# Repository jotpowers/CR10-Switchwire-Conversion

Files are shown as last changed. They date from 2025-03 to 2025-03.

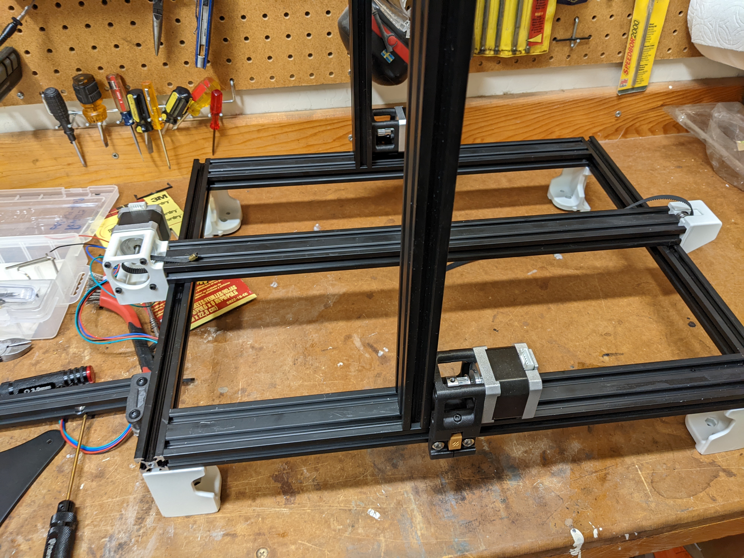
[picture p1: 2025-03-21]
photos/switchwire-test1.jpg

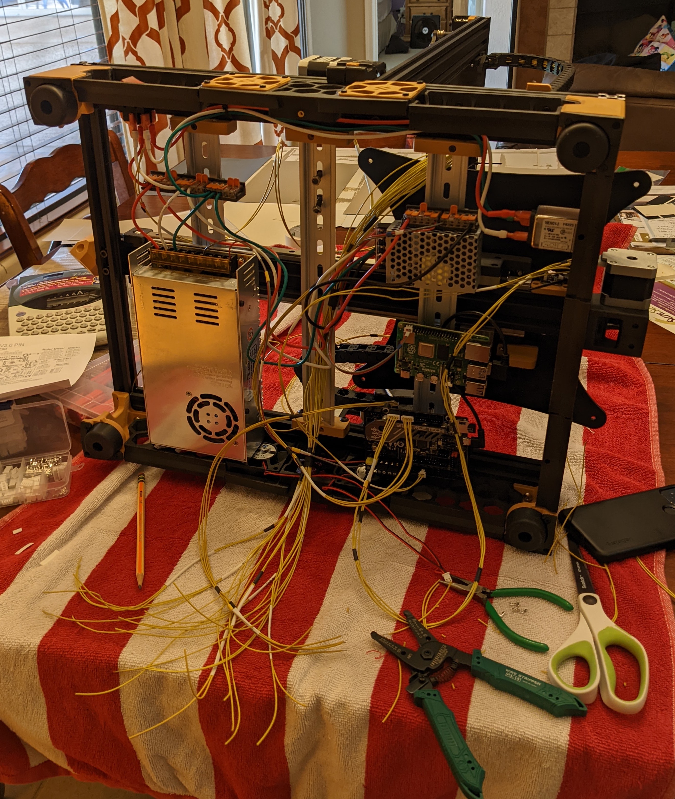
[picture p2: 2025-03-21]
photos/switchwire-electronics-bay-wiring.jpg

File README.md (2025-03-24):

# Introduction

Back in ~2017 my 16 year old son saved his money up and bought and assembled a 300mm Creality CR-10 [1] . It was the first of the post-kickstarter systems, so had some rough edges.  There are plenty of things I don't like about it, but for its cost and time, it's a pretty amazing machine.  When COVID hit and I started printing a bunch of faceshield pieces for Masks4Docs it was a workhorse. But, I kept doing more and more mods to it, but wasn't very reliable.  Finally the SKR controller board (that had replaced the original) broke.  (One day both the bed and hotend thermistors slowly started reading strange numbers).  At that point I was done, and thus began me building a Voron 2.4.

But, I have this perfectly good frame, with motors and some spare parts left over from my 2.4 build...

So I decided to build a CR10, Switchwire.  This repo will be my working notes.

# Design goal

Keep as much of the CR10 stock as possible.  Ideally, you would be able to reverse this mod and have a CR10 back.  Also, ideally, you would never want to.

* Stock frame
* Existing motors  (except extruder, which is going direct drive)
* 12V power supply (which results in a bunch of downstream dependencies)
  * Yeah, this didn't work out.  I couldn't figure out why the fans wouldn't spin up and various other issues.  Turns out, even when turned all the way up, this 12V power supply was putting out like 10.3V.  I replaced it with [this one from Amazon.](https://www.amazon.com/dp/B0131UU9E2?ref_=ppx_hzsearch_conn_dt_b_fed_asin_title_1)
* DC bed heater 

But, I'm not going to be unreasonable here.

* I had already replaced the stock CR10 hotend a long time ago.  I'll go with Afterburner/Stealthburner here.
  * I went with Stealthburner as well as TAP.
* Going to run klipper
  * This means I need a Raspberry Pi
  * Also I'll probably have a dedicated 5V power supply

# Status as of 2022

* The electronics are mostly working and I have a "wire harness" in.
* Hotend is assembled, but not wired up.
* Klipper boots and is happy
* Can buzz all the motors
* Have temperature from both thermistors
* Can heat the bed

# Current status (as of March of 2025)

Well, that was a slow couple of years.  Just got to the annoying debug/triage part and it just sat around.  But my son was in town and we wanted to try to get TPU printing, so pushed forward.

* It's pushing plastic!  

# Progress Pictures
You can see the progress over in the [progress pics](progress.md).

# Upcoming problems

* Bed height/leveling is going to be an issue.  Can't pull the bed down too low against the springs because the bolts can hit the cable chain.  Might need shorter bolts.
  * Think I solved this.  Need to document.

# Things to document
* Thicker XZ pulley's created
* Find power supply holders
* The TAP switchwire mount

# Iteration

Initially I was going to try to reconfigure the frame to get as close to the default SwitchWire as possble.  But that was resulting in some compromises and would have resulted in drilling the existing frame a few times.  Not a deal breaker since extra holes wouldn't prevent it from being reversible, but the orientation of the frame pieces also ended up resulting in challenges with how things would mount and probably having to go modify most of the XZ axies.  

Then someone on Discord had mocked up a SwitchWire with the original frame configuration, and used the Trident feet/skirts.  That had the advantage of making the XZ pretty stock, and only requiring mods to the Y.  There were already some mods that did something similar, so went down that route.

# Y-axis

I'm going to use the [Ender_SW](https://github.com/boubounokefalos/Ender_SW) mod for this.  The reason is that I don't have a spare 2020 aluminum extrusion to run the stock SwitchWire, and I was starting to run into all sorts of issues trying to go with 2040 aluminum extrusion that is from the CR10 frame.  Since that's closer to the stock CR10 and it simplifies XZ axis, I opted to mod the Y-axis and go stock on the XZ axis.  Especially since this Y-axis mod is a two linear rail setup, which has to be twice as good as one, right?

* You do want to add stops for the Y-axis lineral rails since the expectation was they go until they hit the front idler, and that's what prevents the carriages from coming off the rails.  I just printed some extra Z-axis stop pieces and put them at the front.

## Things you have to change

* You need to use an m5 tap on the ends of the Y-axis gantry 2040 aluminum extrusion.  Maybe not need, but it's what I did.  It helps with the motor/idler mouting.
* You'll need to drill holes in the bed plate to center it on the new gantry.  See the [progress photos](progress.md).

### Problems this causes for you

* This whole system sits lower than the stock Switchwire.  
  * This means that the carriages will now sit lower than the deck plate you want to install (to get cereal'd).  
    * My solve this this was to modify the DIN rail mounts to allow the DIN rails to be lower.  I should probably have just CAD'd them from scratch, but I didn't, so they have some small bits of extra "character"
      * But, this now meant that if you use the (new and better) Trident DIN mounts, the 12V power supply sits lower than where the bottom panel lines up.  
        * So, I used the (inferior but shorter) 2.4r1 PS DIN mounts to recover that height.

# XZ-axis

The first problem here is that the existing 2020 that used to hold the X-axis is too wide.  If you try to reuse it, then the belts from the motors would hit it.  So you'd have to modify the motor mounts to go further out.  Then, the pulleys at the top need to be modified.  Then... I decided I wasn't ready for that level of modification yet.  So, you can either chop down your existing 2020 (which is *not* reversible) or order a new one.  

## How I solved this
* I bought a 38cm piece of 2020 extrusion from Misumi.  I might have measured that after a few drinks though, because I should have bought a 39cm piece of 2020 extrusion.  It works, but now you know.

Well, while I was waiting for StealthBurner to come out of beta so it could have a toolhead PCB so I didn't have to wire things, I decided to finally just belt up XZ, because it would be easy.  This is the first place that the difference between 2020 and 3030 has bitten me (that I know of so far).  It makes subtle changes in alignment, so that suddenly the belt wouldn't line up from the top Z idlers down to/past the X gantry.

## How I'm hoping to solve this (because I haven't yet)

I went ahead and pulled the piece out of the cad and then created a parameter for thickness and added 10mm.  It's a big chonky thing, and I now need longer bolts, but it looks like it will work.  It's so ugly though, will probably need a redesign.  Given that, haven't added CAD and STL, but available upon request.

# Below the belt (aka skirts & electronics)

* Went with Trident feet to get height
* Will need to figure out skirts, especially since I went with a split switch and power inlet, because I hate reaching around.  Take that however you will.
  * I went ahead and did this, and I can tell you it was worth it.  The side switch should be stock.

In general the footprint is really close to the 250mm Trident for the front and back, and the 350mm Trident for the sides.  

## What I did

### Rear skirts
* Split the power inlet from the switch.  
  * I could have just blanked out the switch, but that would have looked meh, so I decided to have it be a keystone slot instead.  But, if you look at the CAD on the keystone slots, it's a bit more finicky than you would expect (not just rectangular holes), so instead I blanked one of those and then put the power inlet there. 
    * This means the power switch is now on the right (as you look at the machine), so to use the original keystone plate, you need to mirror it to be on the left.
  * The footprint is a little narrower than the 250, so I scaled the center rear panel (unlocked, so only one dimension) from 117mm to 100mm on the X axis.
    * But, things you don't think about.  The bolts for the center rail run through the middle of this extrusion.  Your drop in nuts won't hit it, but the slight raised part on the skirt, meant to slide into that slot, now slightly hits those bolts.  Means that you end up having to work a little extra hard to get the bolts in that hold that piece of the skirt.

### Side skirts

* I filled and then cut the front right skirt to include the switch.  Yes, I'm glad I did it, having the switch easy to access is so much better.
* The footprint is again, slightly smaller, so I scaled one of the skirt pieces down to ~124mm in the long axis to get it to fit.
* I *despise* VHB tape, so I went with the new (2.4r2) mounts for the fans and the blank fan pieces.  This works great, except...
  * The mounts for the A/B motors interferes with the fan cover in one of the corners of one plate on each side.  It's not elegant, but I just trimmed and filed that to allow it to fit in.  Was able to screw them in with flat head screws, but it's a bit hacky. (Visible in the [progress picks](progress.md))

### Electronics

I had a 1 meter piece of DIN rail.  Since the space is 32cm (I think) across, I actually went with three, and have the center one with a cable raceway to make it all nice and pretty.

Note on cable raceway: I tried the printed ones, but ABS is just too brittle for them and they would break, so broke down (heh) and bought them from Amazon.

# Extra/modified CAD items

* Wago mount for bed wiring
* Lowered DIN mounts
* Side skirt with switch
* Back power inlet
* Y-axis tensioner, now with more attitude
* More linear rail stops
* SKR holder for DIN mount

# Stuff you have to buy

* 20t pulley
* gates 6mm belt (had this as a spare from 2.4 build)
* bearings
* various screws (will probably detail later)
* filament (for printing parts)
* Keybak (13 oz)
* linear rails
* wire (wow, a lot of it)
* cable chains
* heatsets
* 5 MGNH12 rails.  
  * The biggest I could find easily were 400mm.  On Z I think you could go to 450, so maybe in the future I'll change that since it would just be a rail swap and not much other change. 
  * You need 4x 400
  * 1x 350 for the X axis gantry
* JST-PH 2.0 connectors (for motors) [Amazon link](https://smile.amazon.com/gp/product/B09DBHG6NW/ref=ppx_yo_dt_b_asin_title_o07_s00?ie=UTF8&psc=1)

## Stuff you might have
* Blue loctite

## Not really necessary, but I did anyway

* 5v PSU
* Power inlet and switch

# CAD

In general my goal is to change as few things as possible.  I might actually copy all of the CAD files here in the future to simply give you one place to download them, but not for now.  But, here are a list of things I changed:

* [Stealth Idler](STL/y-gantry/ender_sw_stealth_idler.stl)
  * I provide the f3d and step files.  This mod addressess two issues:
    * I wanted to be able to put screws into a threaded m5 hole in the 2040
    * I did not like the look of the standard idler.  Given the recently released StealthBurner, I figured I'd do a bad version of that for the outer idler.  The inner remains unchanged.
* [Mounts](STL/mounts/)
  * Because the Switchwire assumes you're mounting everything to the extrusions, and I'm using DIN, I needed a bracket for the SKR to mount to the DIN holder.  This bracket isn't perfect, but it's close enough for now.
  * Also, while I was at it, I made one for an Arduino Uno.  This is really to be a secondary MCU for my 2.4, but I'm putting it here for now, because why not.
* [Offset DIN mount](STL/mounts/offset-din-rail-mount.stl)
  * As described above, in the "cascading consequences" of the Y-axis, here are the files for the offset DIN mounts.  A little ugly because I didn't want to have to CAD in the profile of the DIN rail.  I should really learn how to start with a body to make that easier.
* [Power Skirts](STL/skirts)
  * This contains the files for both the power inlet (with keystone) and the (right) side skirt with a hole for the switch.  I made some minor mods on the power inlet after I printed mine, to correct some issues, but haven't printed/tested it, so buyer beware.

# Helpful Hints

* There is currently a SKR Mini E3 V3 config file for the switchwire.  As a result, when you get done fixing various pin definitions in printer.cfg, klipper just shuts down complaining about ADC pin.
  * I think it's the sensor pin on the heater bed that changed between V2 and V3.  New sensor pin is PC4.

* I am inordinately happy with the fact that I have the original CR10 display working now. It has terrible resolution.  It's a bad size.  But I love it because it maintains the original (even if I now have to go buy/make a longer ribbon cable).  Here are the values I used for the config to get the display to work.  

<pre>
[display]
lcd_type: st7920
cs_pin: PB8
sclk_pin: PB9
sid_pin: PD6
encoder_pins: ^PA10, ^PA9
#encoder_pins: ^EXP1_5, ^EXP1_3
click_pin: ^!PA15
#kill_pin: ^!EXP2_8

[output_pin beeper]
pin: PB5
</pre>

# Notes

[1] Officially it's CR-10, not CR10, but no one really cares and the latter is more commonly used, so I'll go with that going forward.  Or randomly.

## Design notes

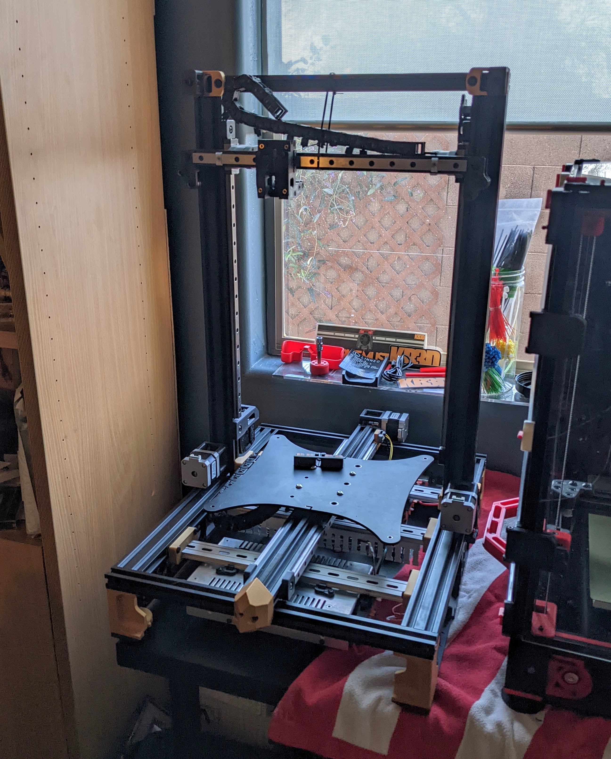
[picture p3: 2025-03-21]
photos/switchwire-electronics-mounted.jpg

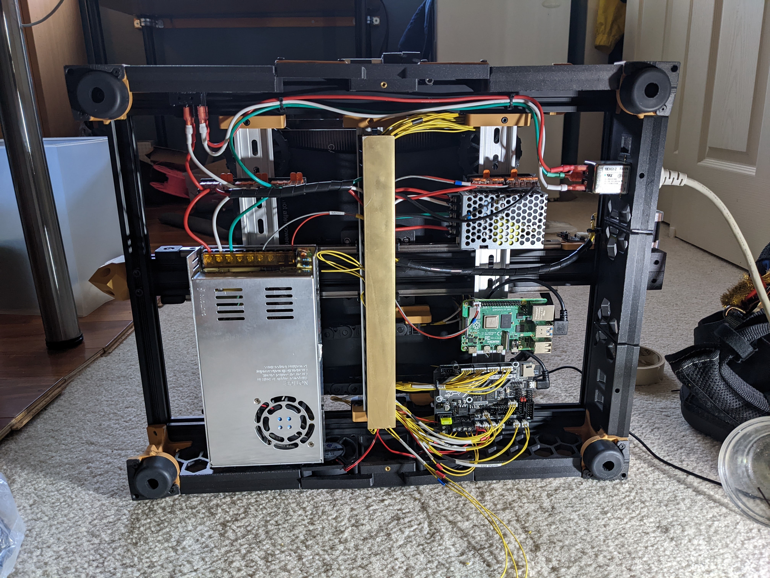
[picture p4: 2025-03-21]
photos/switchwire-electronics-bay-2.jpg

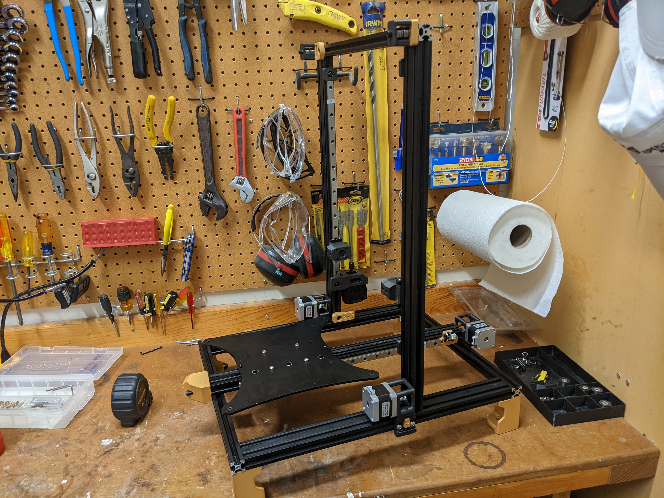
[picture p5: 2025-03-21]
photos/switchwire-plate-mounted.jpg

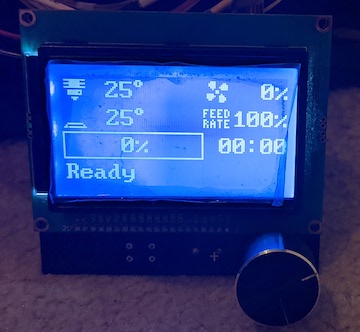
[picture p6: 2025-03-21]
photos/switchwire-cr10-display.jpg

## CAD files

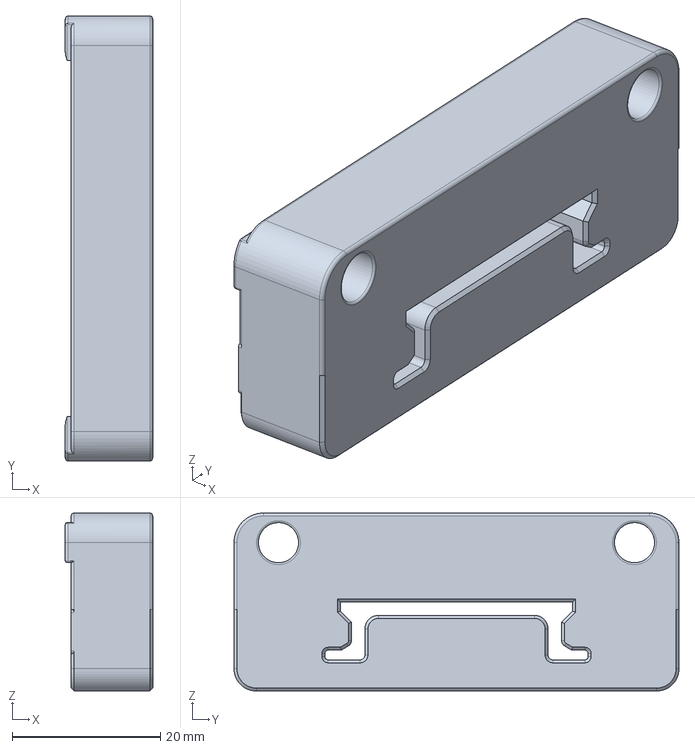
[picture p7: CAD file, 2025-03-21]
CAD/mounts/offset-din-rail-mount.step
11.8 x 60.0 x 24.0 mm
DIN_Mount (1)
DIN_Mount (2)

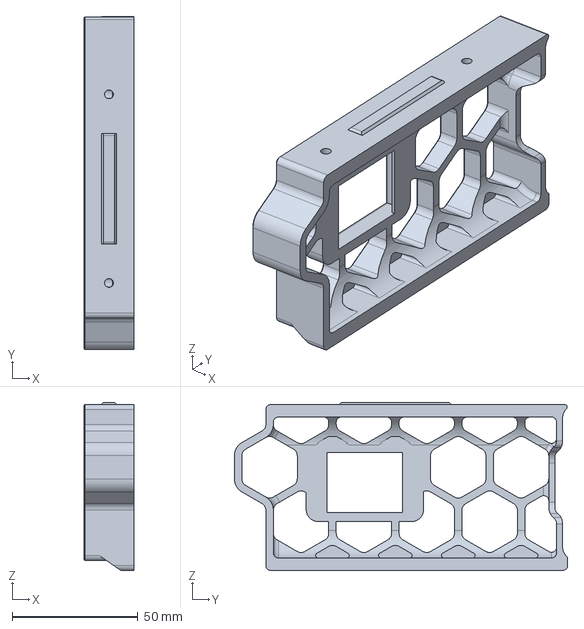
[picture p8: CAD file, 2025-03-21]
CAD/skirts/switchwire-switchskirt.step
20.0 x 132.5 x 66.8 mm

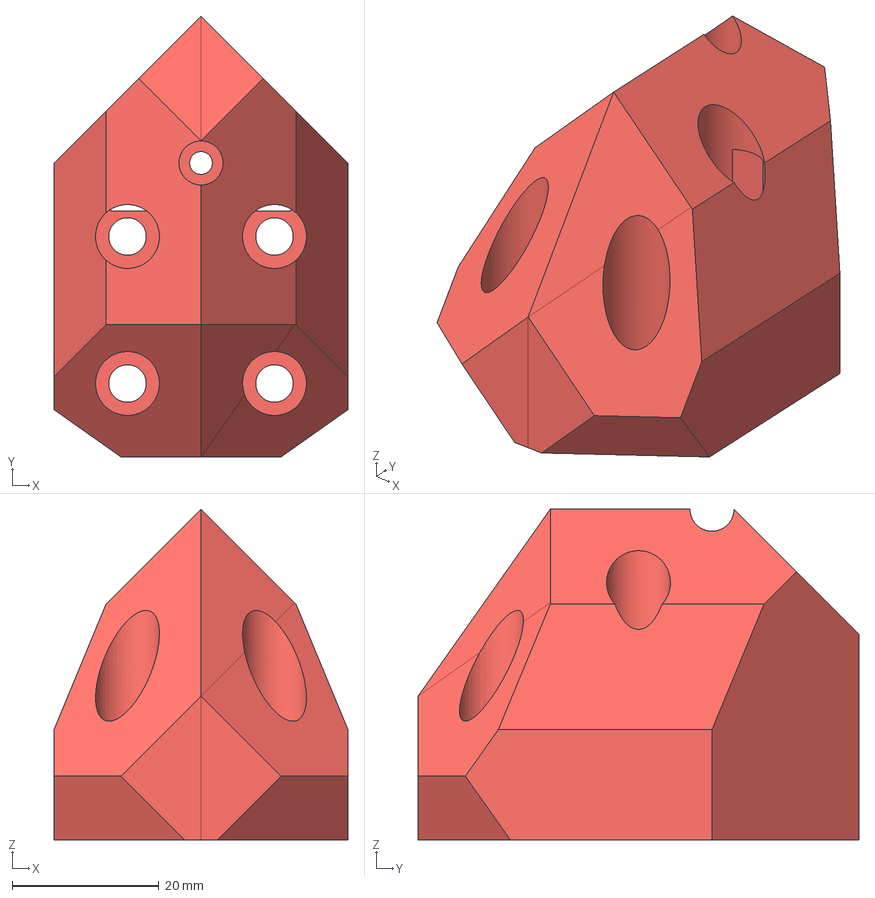
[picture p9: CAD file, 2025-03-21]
CAD/y-gantry/ender_sw_stealth_idler.step
40.0 x 60.0 x 45.0 mm

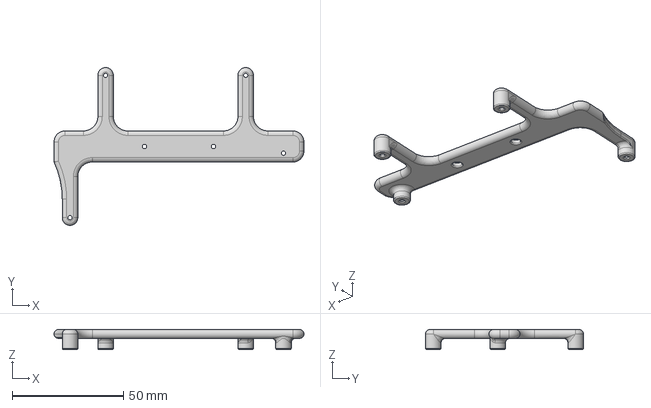
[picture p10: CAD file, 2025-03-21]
CAD/mounts/skr-mini-e3-v3-mount.step
112.4 x 71.0 x 9.00 mm

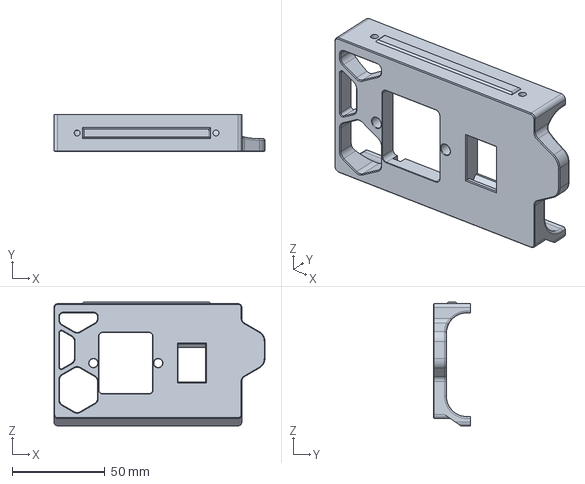
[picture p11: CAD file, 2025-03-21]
CAD/skirts/switchwire-power-inlet.step
114.0 x 20.0 x 66.8 mm

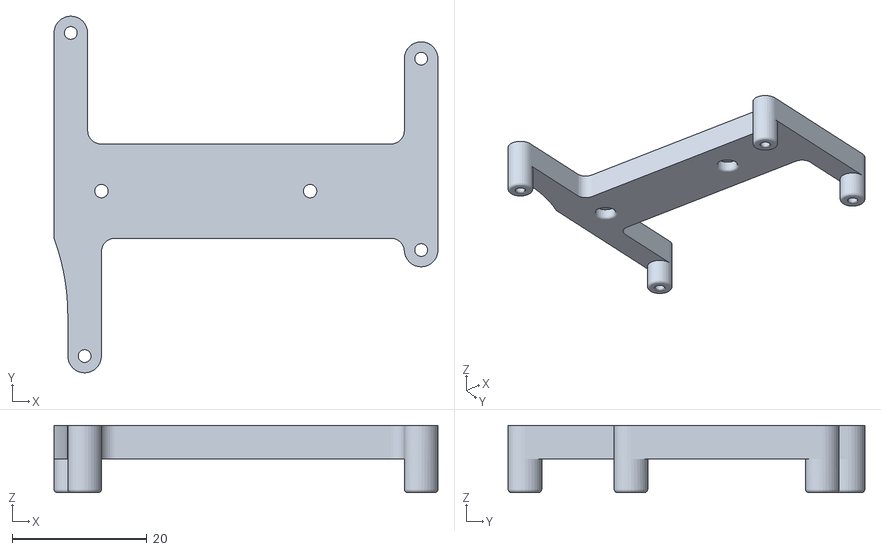
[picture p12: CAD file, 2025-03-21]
CAD/mounts/arduino-uno-mount.stl
57.1 x 53.0 x 10.0

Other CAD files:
CAD/mounts/arduino-uno-mount.f3d
CAD/mounts/offset-din-rail-mount.f3d
CAD/mounts/skr-mini-e3-v3-mount.f3d
CAD/skirts/switchwire-power-inlet.f3d
CAD/skirts/switchwire-switchskirt.f3d
CAD/y-gantry/ender_sw_stealth_idler.f3d
STL/mounts/arduino-uno-mount.stl
STL/mounts/offset-din-rail-mount.stl
STL/mounts/skr-mini-e3-v3-mount.stl
STL/skirts/switchwire-power-inlet.stl
STL/skirts/switchwire-switchskirt.stl
STL/y-gantry/ender_sw_stealth_idler.stl
